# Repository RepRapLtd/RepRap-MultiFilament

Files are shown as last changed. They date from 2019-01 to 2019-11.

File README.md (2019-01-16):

# RepRap-MultiFilament
Multi filament drive for RepRap and other FFF printers

The drive has three components:

  1. Multi-drive - a pinch-wheel drive for multiple filaments driven by a single stepper and a small DC motor.
  2. Guillotine - a device that cuts filament driven by the same small DC motor.
  3. Filament-Y - a passive device that merges feeds of filament into a single Bowden channel.

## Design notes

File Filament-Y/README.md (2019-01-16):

# Filament-Y
A design for a 3D printer filament merging Y for multiple-material RepRaps

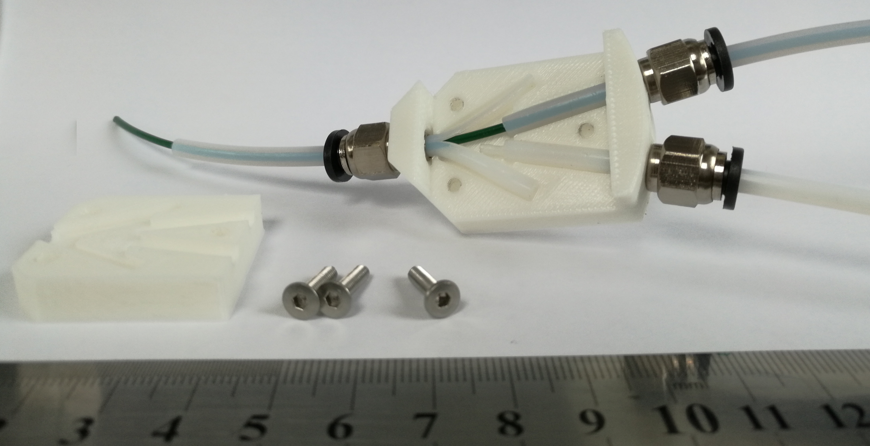
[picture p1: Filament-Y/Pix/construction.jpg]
How it goes together


This design is based on a wonderfully simple idea from Martin Zeman (see: https://www.thingiverse.com/thing:3039887).  It is easy to print, to construct, and to put together.  In operation it works very smoothly with low friction.

Two input 4mm PTFE Bowden feeds come straight through the pneumatic fittings on the right of the picture (like these: https://reprapltd.com/shop/pneumatic-fitting/ ; make sure you get the ones where the tube goes right through).  You split the end of the output tube down the middle to a depth of 20mm then push it through, guiding the two halves of the split to their retaining slots left and right.  Finally screw the top down with three 12mm M3 countersunk screws.  These self-tap into the base.

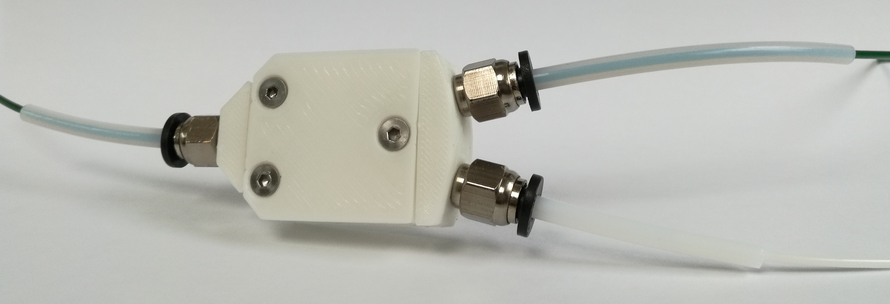
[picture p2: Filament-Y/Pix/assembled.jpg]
Assembled


Here it is assembled.

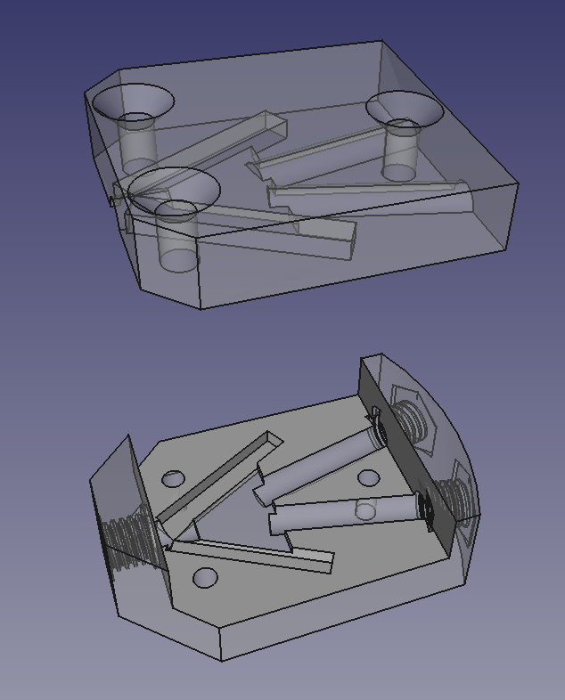
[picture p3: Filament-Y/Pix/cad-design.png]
CAD design


The CAD design was done in FreeCAD (https://www.freecadweb.org/).

You can, of course, chain these together to merge as many filament streams as you wish.

This is the first in a set of modular designs that together will form a multi-filament drive system.  The idea is that you will be able to put them together to form a drive system that will be an add on to any system to feed into a single nozzle.  All the system will need to be able to do is to drive one stepper for them all, and send either serial data or a number of parallel bits to give the number of filaments (1 bit: 2 filaments; 2 bits 4 and so on).

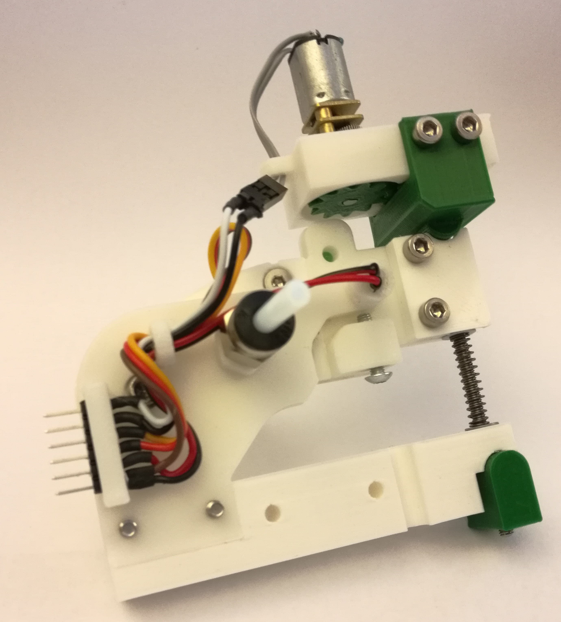
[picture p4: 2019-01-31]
Pix/wired-guillotine.jpg

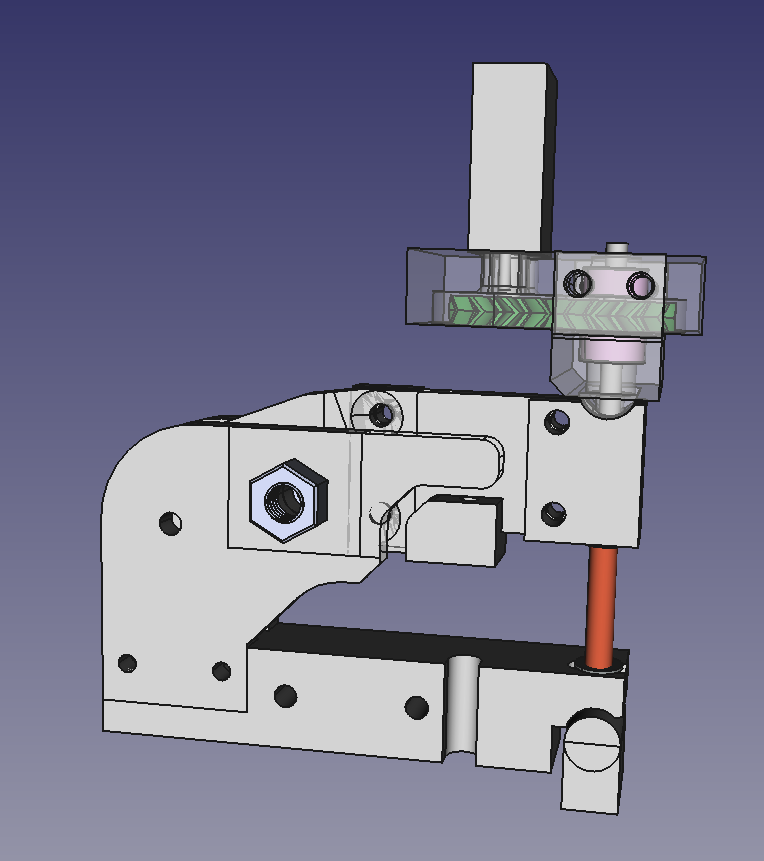
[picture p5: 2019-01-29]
Pix/cad-guillotine.png

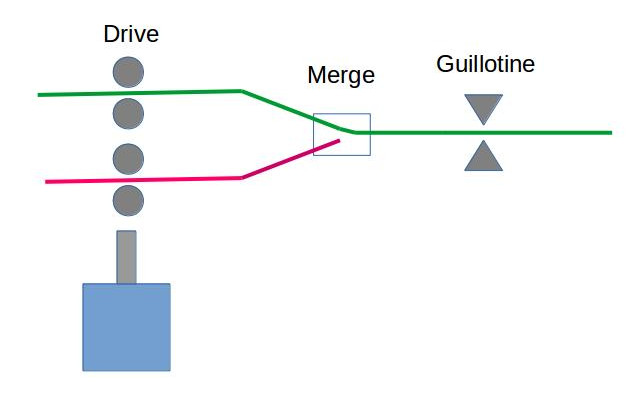
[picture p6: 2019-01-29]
Pix/how-it-works.jpg

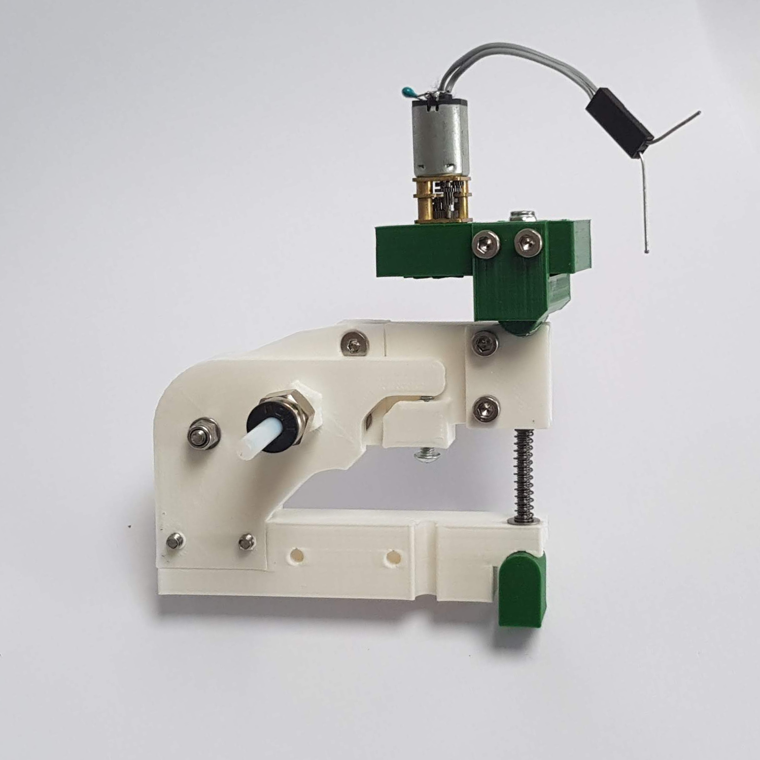
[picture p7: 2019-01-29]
Pix/guillotine-photo.jpg

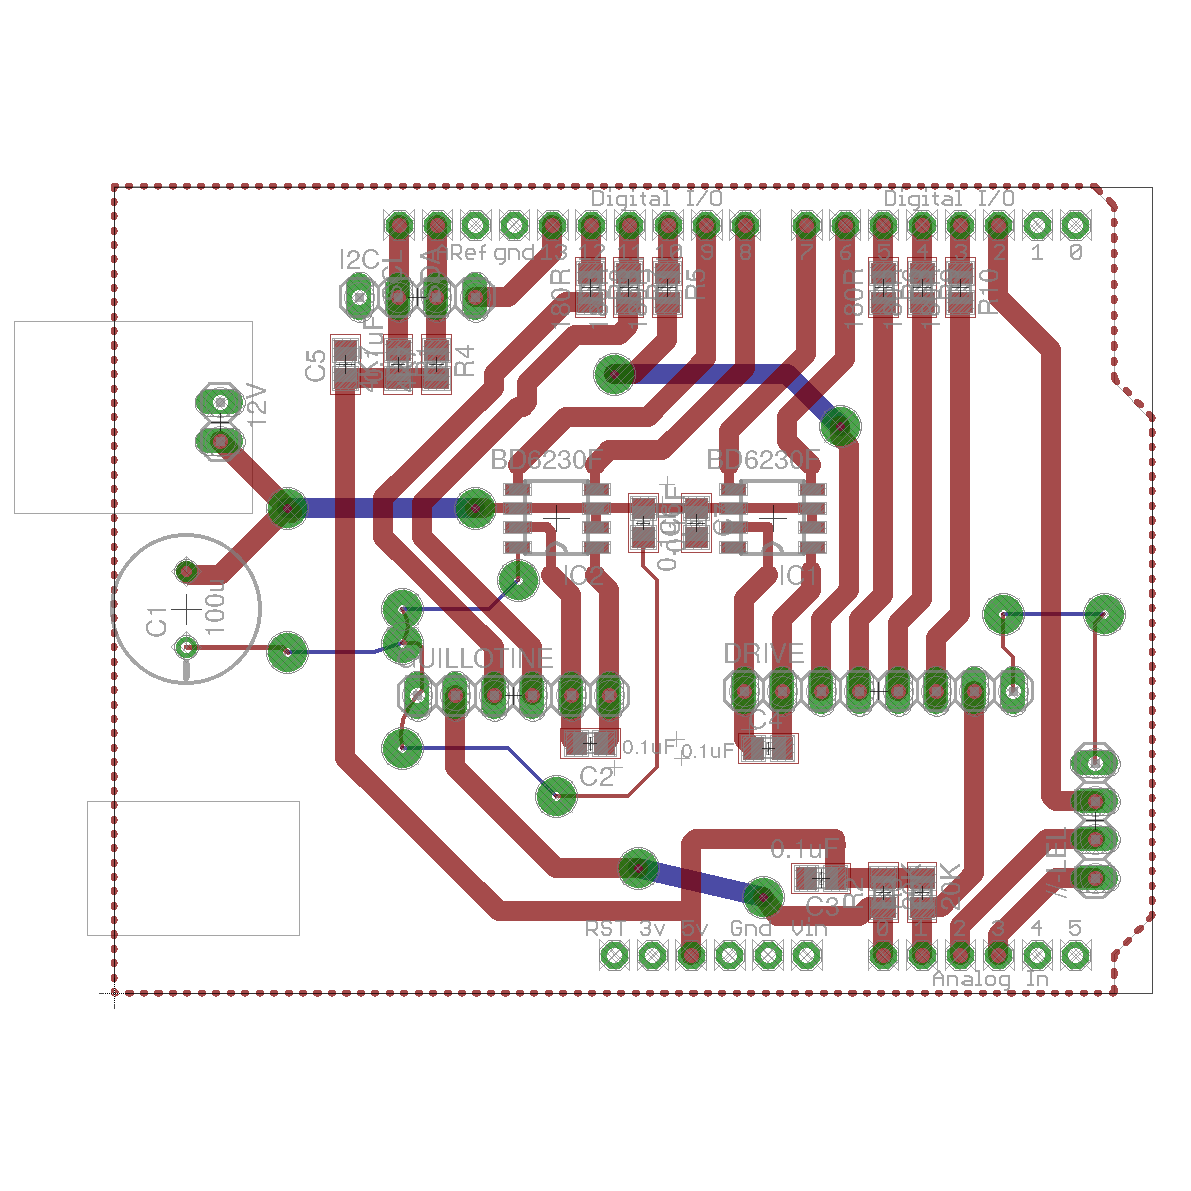
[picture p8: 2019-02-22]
Pix/circuit.png

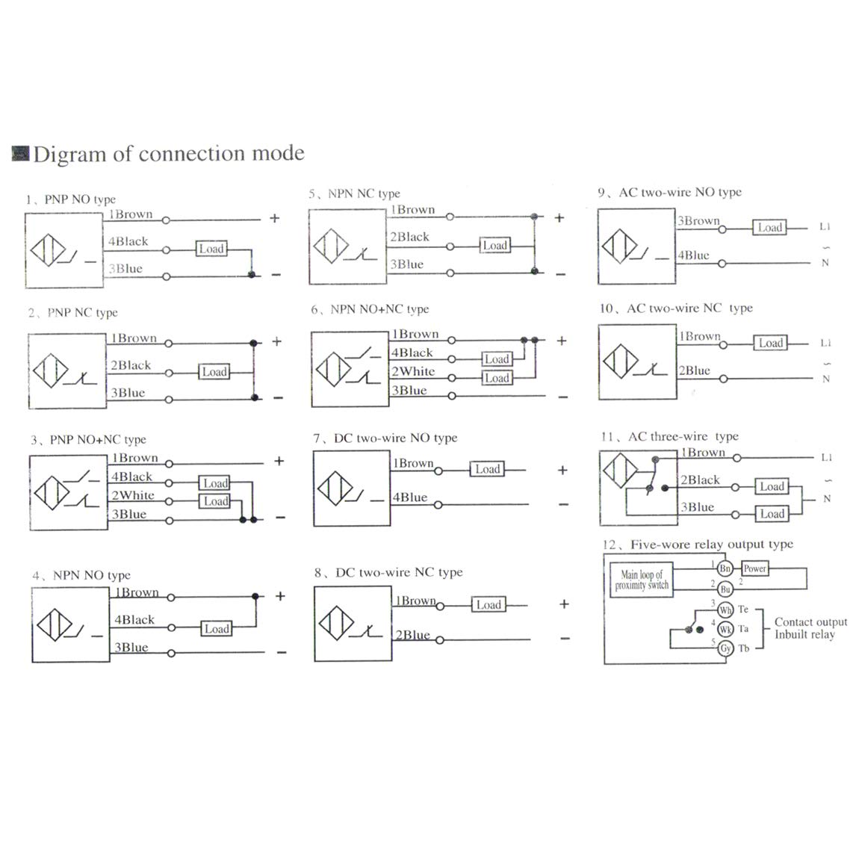
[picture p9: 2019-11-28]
Prusa/mag-sensor2.jpg

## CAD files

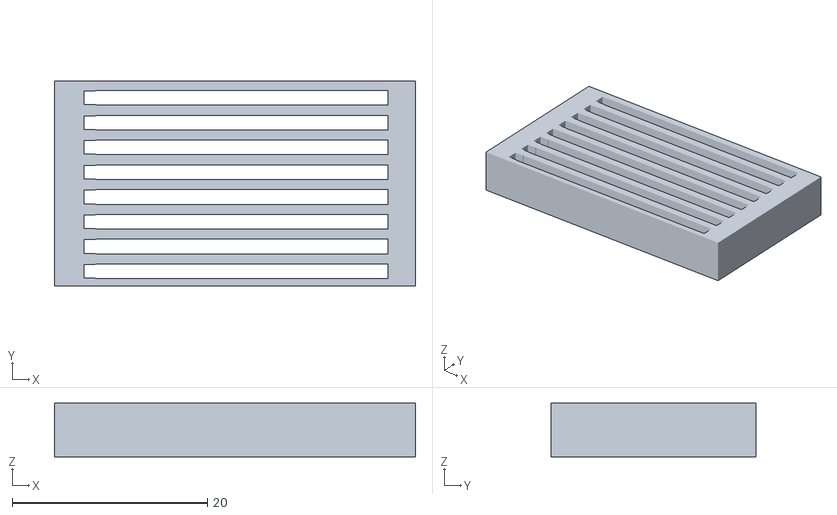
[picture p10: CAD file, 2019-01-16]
Experiment-and-tests/V3 1.2 Main Body.stl
37.0 x 21.0 x 5.50

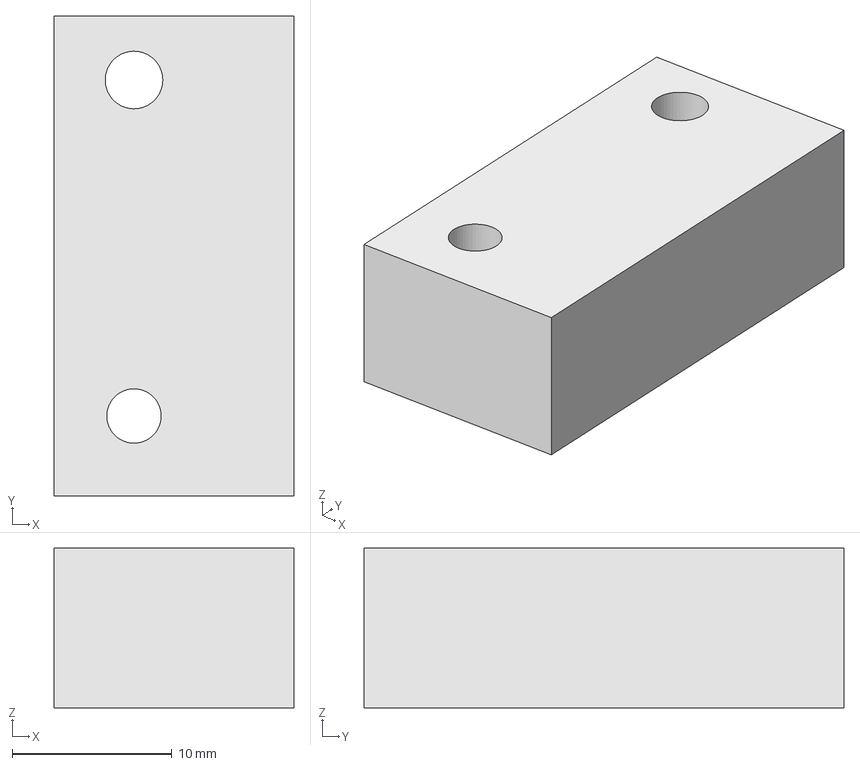
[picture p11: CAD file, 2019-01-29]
Experiment-and-tests/photo-led-test.fcstd
15.0 x 30.0 x 10.0 mm

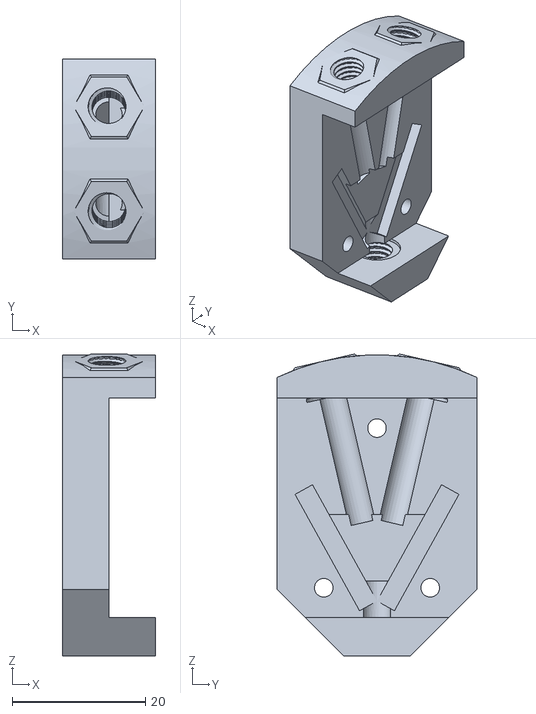
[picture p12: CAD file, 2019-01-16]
Filament-Y/Mechanics/STLs/Y-base.stl
14.0 x 30.0 x 45.4

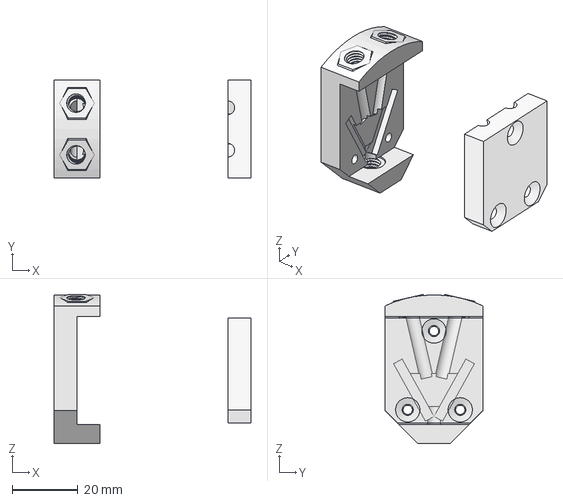
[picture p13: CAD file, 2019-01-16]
Filament-Y/Mechanics/y.fcstd
60.0 x 30.0 x 45.4 mm
base
top

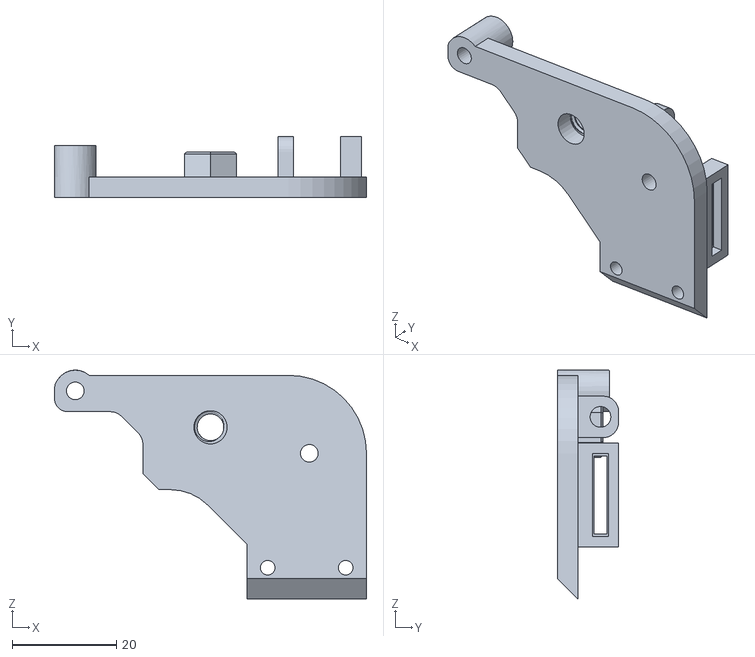
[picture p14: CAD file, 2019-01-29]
Guillotine/Mechanics/STLs/bearing-support-2.stl
60.0 x 11.8 x 44.0

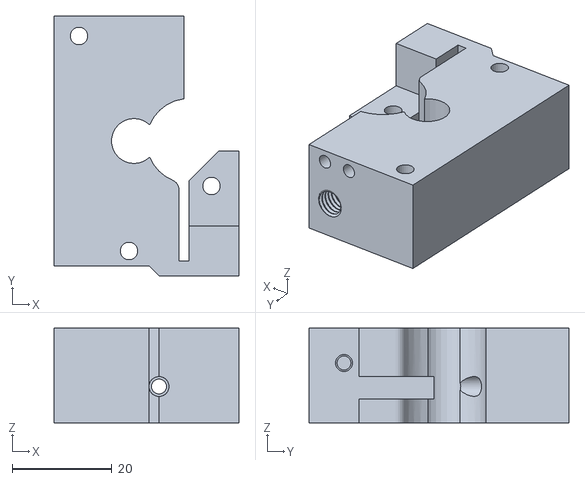
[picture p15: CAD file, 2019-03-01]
Multi-drive/Mechanics/STLs/drive-block.stl
37.0 x 52.0 x 19.0

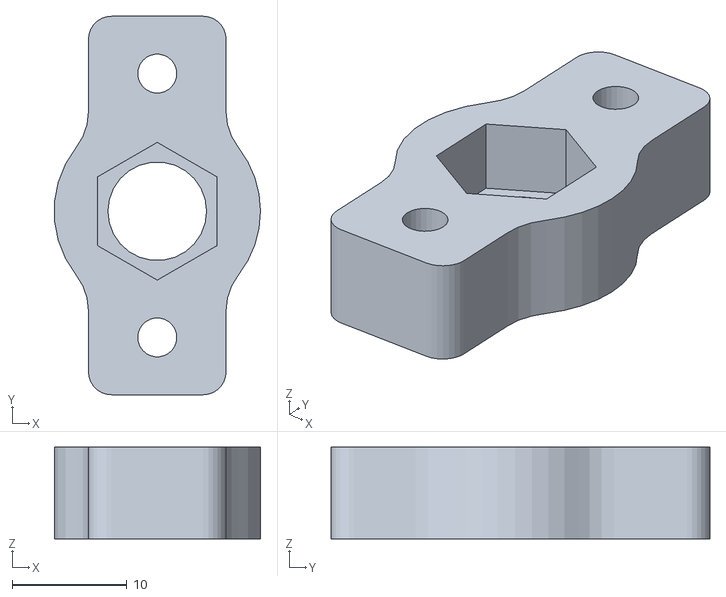
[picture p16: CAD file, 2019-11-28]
Prusa/pneumatic-holder.stl
18.0 x 33.0 x 8.00

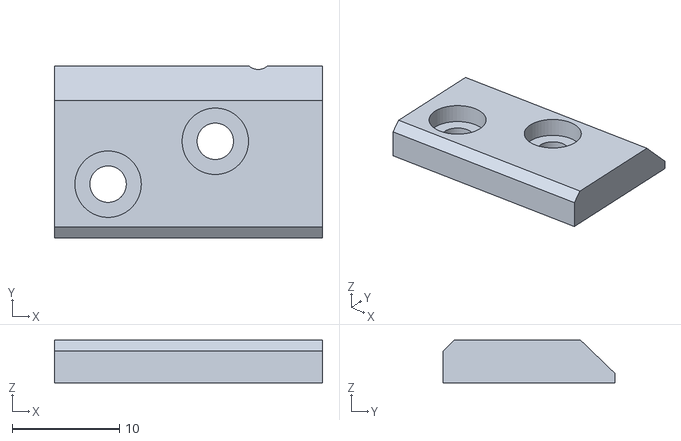
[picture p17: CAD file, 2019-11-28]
Prusa/Prusa MMU/STLs/mmu2-blade-holder.stl
25.0 x 16.0 x 4.00

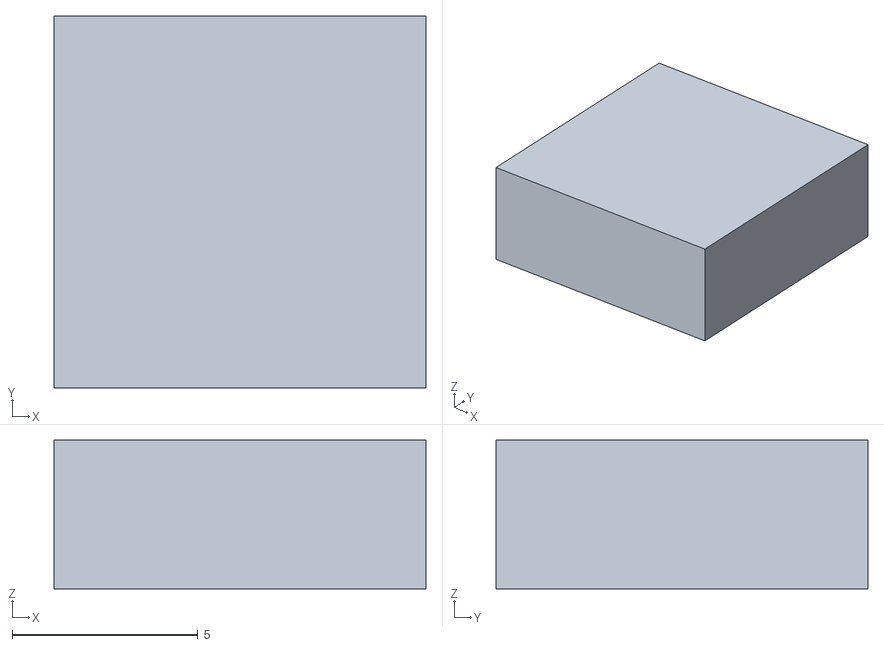
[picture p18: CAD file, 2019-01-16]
Experiment-and-tests/simple-testblock-green.stl
10.0 x 10.0 x 4.00

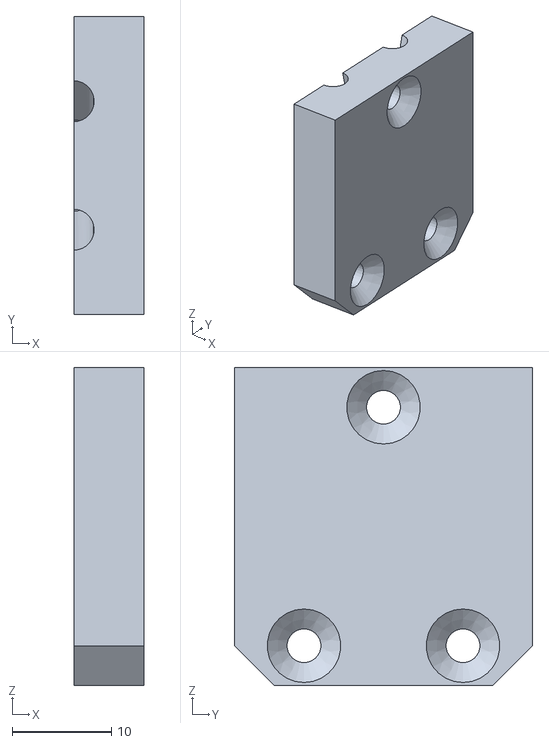
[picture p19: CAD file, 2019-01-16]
Filament-Y/Mechanics/STLs/Y-top.stl
7.00 x 30.0 x 32.0

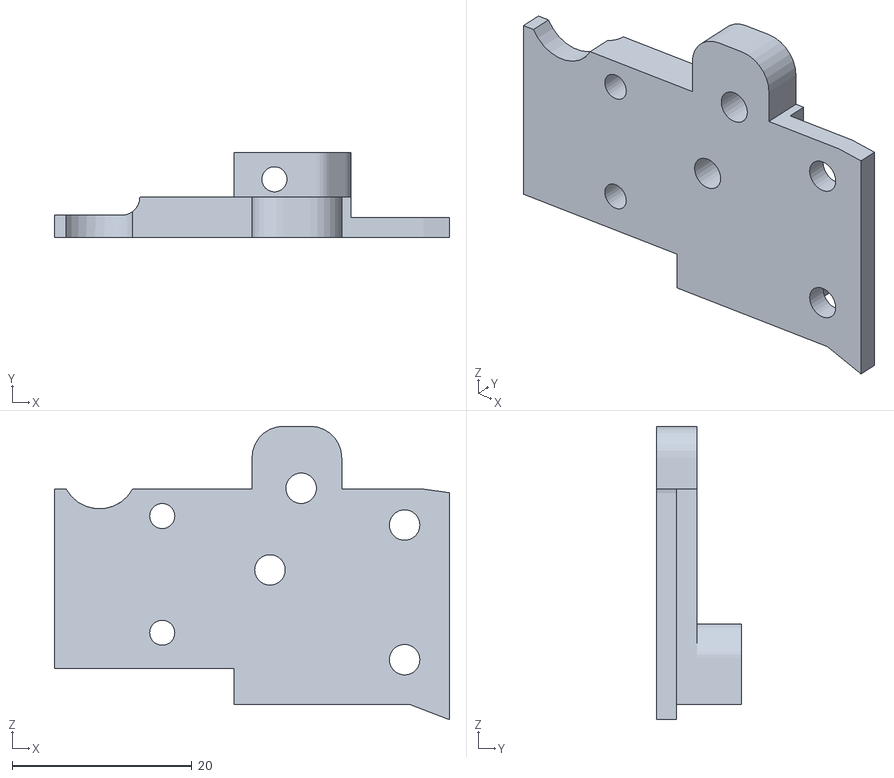
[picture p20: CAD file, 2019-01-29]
Guillotine/Mechanics/STLs/cutting-arm-extension.stl
44.0 x 9.50 x 32.7

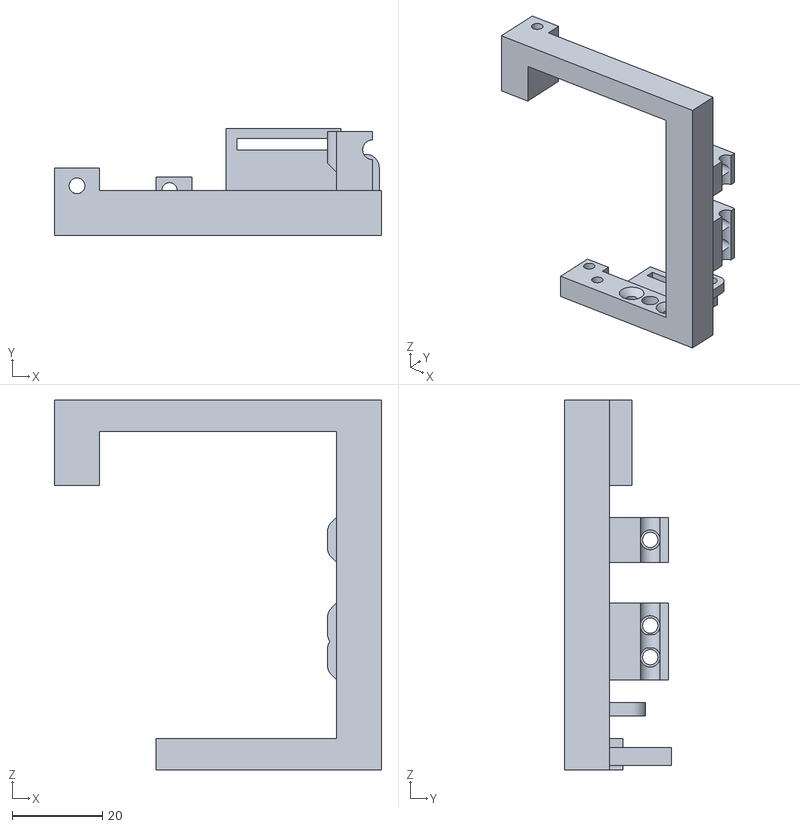
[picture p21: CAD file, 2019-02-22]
Multi-drive/Mechanics/STLs/track.stl
72.5 x 23.7 x 82.0

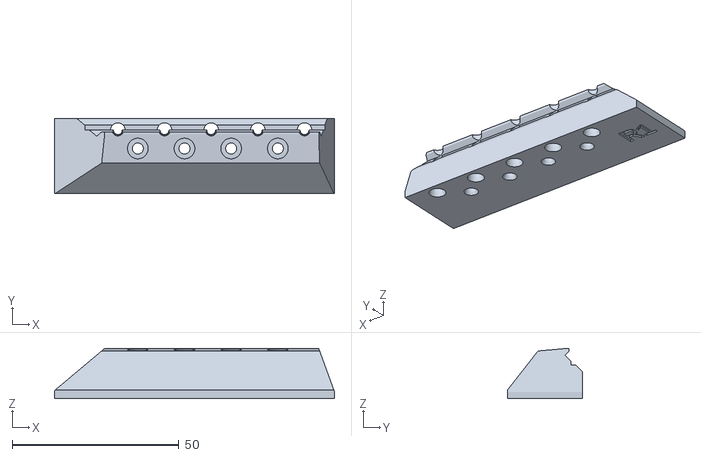
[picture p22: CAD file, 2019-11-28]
Prusa/Prusa MMU/STLs/mmu2-front-PTFE-holder.stl
84.0 x 22.5 x 15.0

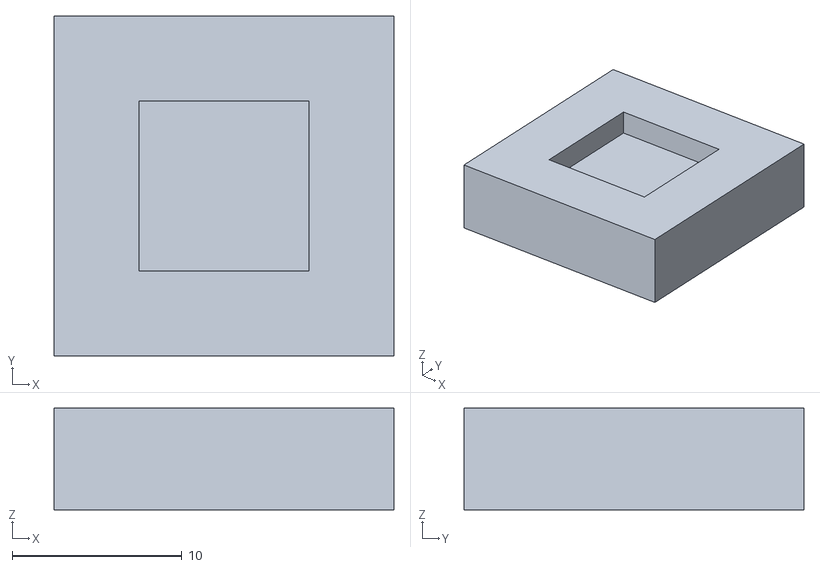
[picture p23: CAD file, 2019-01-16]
Experiment-and-tests/simple-testblock-white.stl
20.0 x 20.0 x 6.00

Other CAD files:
Experiment-and-tests/V2 1.6 Main Body.stl
Experiment-and-tests/V1 0.8 Main Body.stl
Guillotine/Mechanics/STLs/clamp-plate.stl
Multi-drive/Mechanics/STLs/motor-gearbox-mount.stl
Experiment-and-tests/External Thread.stp
Experiment-and-tests/Internal thread.stp
Experiment-and-tests/Test Piece V1 0.8.fcstd
Experiment-and-tests/Test Piece V2 1.6.fcstd
Experiment-and-tests/Test Piece V3 1.2.fcstd
Experiment-and-tests/V1 0.8 Conducting Filament.stl
Experiment-and-tests/V2 1.6 Conducting Filament.stl
Experiment-and-tests/V3 1.2 Conducting Filament.stl
Experiment-and-tests/force-test.fcstd
Experiment-and-tests/photo-led-test.stl
Guillotine/Mechanics/STLs/Legacy/bearing-clamp.stl
Guillotine/Mechanics/STLs/Legacy/cut-holder-arm.stl
Guillotine/Mechanics/STLs/Legacy/cut-holder-base.stl
Guillotine/Mechanics/STLs/Legacy/cut-lever-block.stl
Guillotine/Mechanics/STLs/Legacy/cut-lever.stl
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

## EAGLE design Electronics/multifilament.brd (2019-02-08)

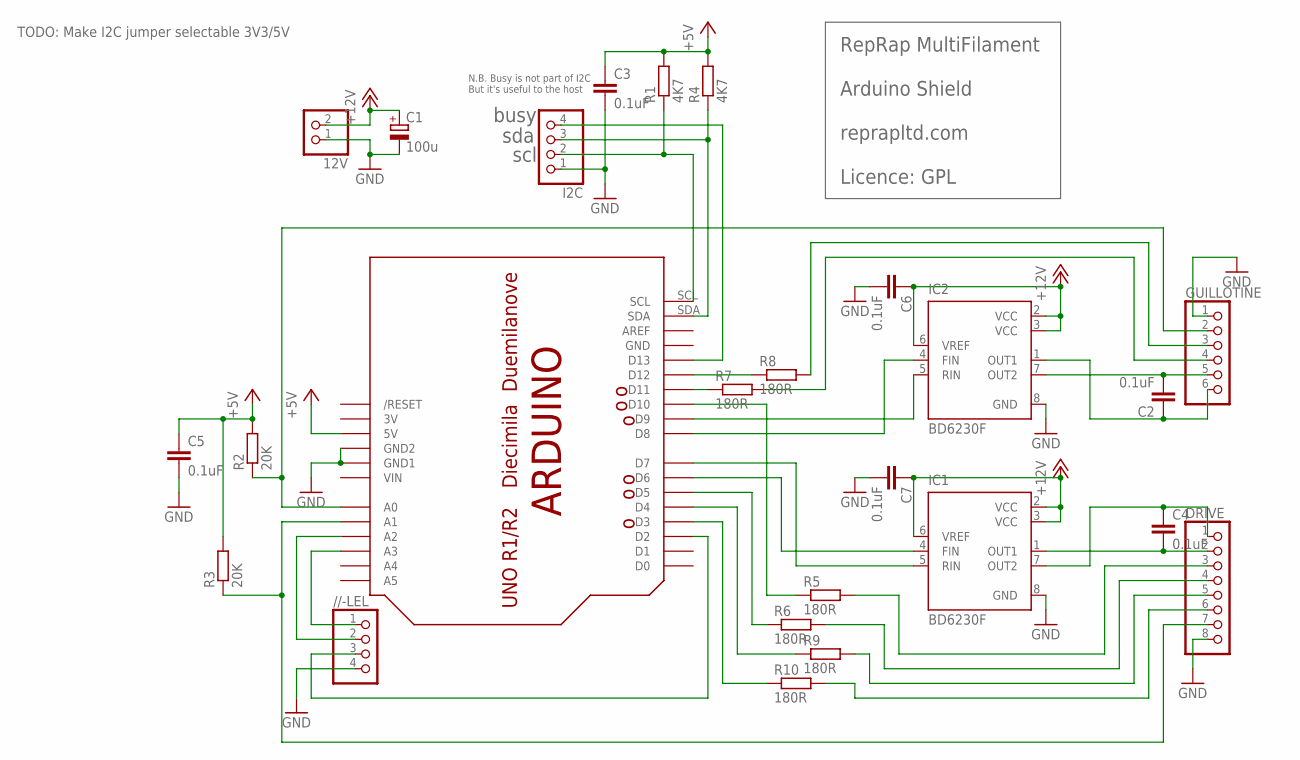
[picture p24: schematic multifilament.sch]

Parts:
12V: PINHD-1X2; 1X02
//-LEL: PINHD-1X4; 1X04
C1: 100u; SANYO-OSCON_9F
C2, C3, C4, C5, C6, C7: 0.1uF; C0805
DRIVE: PINHD-1X8; 1X08
GUILLOTINE: PINHD-1X6; 1X06
I2C: PINHD-1X4; 1X04
IC1, IC2: BD6230F; SOP8
R1, R4: 4K7; M0805
R2, R3: 20K; M0805
R5, R6, R7, R8, R9, R10: 180R; M0805
U$1: ARDUINO-BPLACE

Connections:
3V: U$1.3V
+5V: C3.1, C5.1, R1.2, R2.2, R3.2, R4.2, U$1.5V
+12V: 12V.2, C1.+, C6.1, C7.1, IC1.2 (VCC), IC1.3 (VCC), IC1.6 (VREF), IC2.2 (VCC), IC2.3 (VCC), IC2.6 (VREF)
GND: 12V.1, //-LEL.4, C1.-, C3.2, C5.2, C6.2, C7.2, DRIVE.8, GUILLOTINE.1, I2C.1, IC1.8 (GND), IC2.8 (GND), U$1.GND, U$1.GND1, U$1.GND2
unnamed: I2C.2, R1.1, U$1.SCL
unnamed: GUILLOTINE.2, R2.1, U$1.A0
unnamed: C2.2, GUILLOTINE.5, IC2.7 (OUT2)
unnamed: C4.2, DRIVE.2, IC1.1 (OUT1)
unnamed: R6.1, U$1.D5
unnamed: IC1.4 (FIN), U$1.D6
unnamed: IC1.5 (RIN), U$1.D7
unnamed: IC2.4 (FIN), U$1.D8
unnamed: I2C.3, R4.1, U$1.SDA
unnamed: DRIVE.7, R3.1, U$1.A1
unnamed: IC2.5 (RIN), U$1.D9
unnamed: I2C.4, U$1.D13
unnamed: GUILLOTINE.3, R8.2
unnamed: R7.1, U$1.D11
unnamed: GUILLOTINE.4, R7.2
unnamed: R8.1, U$1.D12
unnamed: R5.1, U$1.D10
unnamed: DRIVE.3, R5.2
unnamed: DRIVE.4, R6.2
unnamed: R9.1, U$1.D4
unnamed: DRIVE.5, R9.2
unnamed: R10.1, U$1.D3
unnamed: DRIVE.6, R10.2
unnamed: //-LEL.2, U$1.A2
unnamed: //-LEL.1, U$1.A3
unnamed: //-LEL.3, U$1.D2
unnamed: C4.1, DRIVE.1, IC1.7 (OUT2)
unnamed: C2.1, GUILLOTINE.6, IC2.1 (OUT1)
VIN: U$1.VIN

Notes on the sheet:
RepRap MultiFilament Arduino Shield reprapltd.com Licence: GPL
busy
sda
scl
N.B. Busy is not part of I2C But it's useful to the host
TODO: Make I2C jumper selectable 3V3/5V

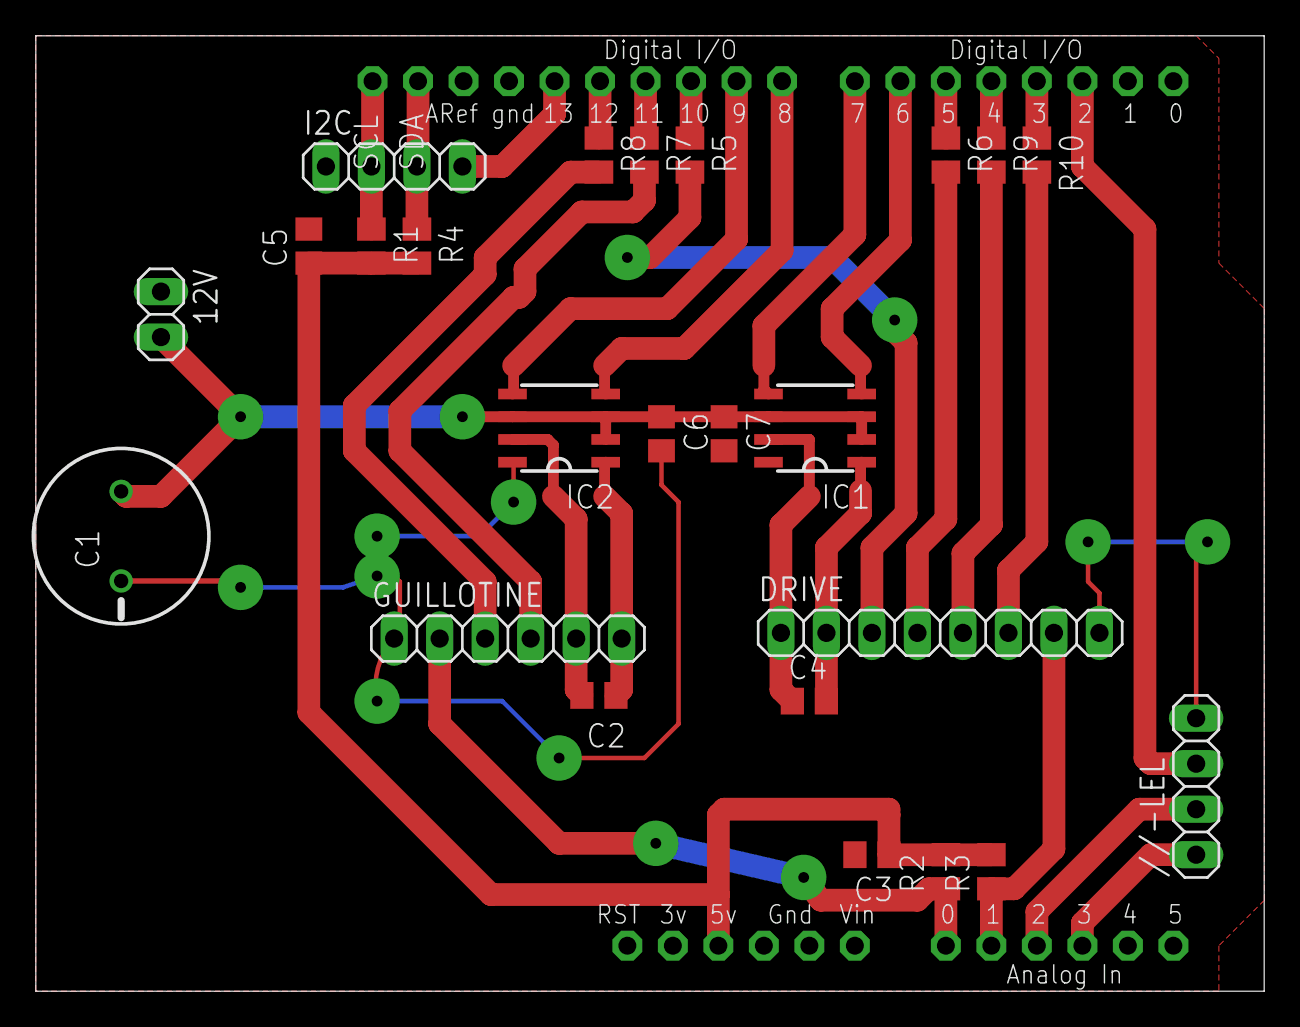
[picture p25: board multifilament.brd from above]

Board: 2 copper layers, 68.6 x 53.3 mm, 25 parts (0 on the bottom side), 31 nets.

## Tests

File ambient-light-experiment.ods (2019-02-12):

Dark | Light | diff
31 | 28 | 3 | 13.2340672 | 10.2340672 | 25.6255748
38 | 30 | 8 | 16.1317788 | 8.1317788
48 | 32 | 16 | 20.2212508 | 4.2212508
124 | 49 | 75 | 49.3744252 | 25.6255748
318 | 195 | 123 | 108.3501148 | 14.6498852
493 | 345 | 148 | 142.5131248 | 5.4868752
548 | 419 | 129 | 149.5208508 | 20.5208508
577 | 445 | 132 | 152.4977008 | 20.4977008
731 | 563 | 168 | 159.9977472 | 8.0022528
756 | 588 | 168 | 159.8960572 | 8.1039428
788 | 645 | 143 | 159.2281788 | 16.2281788
808 | 640 | 168 | 158.5041628 | 9.4958372
864 | 694 | 170 | 155.2222492 | 14.7777508
1003 | 870 | 133 | 139.0855168 | 6.0855168

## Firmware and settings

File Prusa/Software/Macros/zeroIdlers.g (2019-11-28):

; Zero the idler bearings

M906 X800 Y800 Z800 E800:800:800:500
T3
M83
G1 E-10 F500
G92 E0:0:0:0
M906 X800 Y800 Z800 E800:800:800:800

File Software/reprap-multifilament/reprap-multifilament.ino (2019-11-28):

/*
   RepRap MultiFilament Arduino Control Program

   This controls the RepRap Multifilament drive using
   a shield for the Arduino Uno.

   Adrian Bowyer

   RepRap Ltd
   http://reprapltd.com

   Github: https://github.com/RepRapLtd/RepRap-MultiFilament

   Licence: GPL

   7 February 2019
*/

// Arduino Uno Pins

// BD6231 Motor H-bridge chips

const unsigned char driveFIN = 6;      // PWM
const unsigned char driveRIN = 7;
const unsigned char guillotineFIN = 8;
const unsigned char guillotineRIN = 9; // PWM

// Optosensors

const unsigned char guillotinePT = A0;  // Phototransistor
const unsigned char drivePT = A1;       // Phototransistor
const int driveLEDs = 4;
const unsigned char driveLED[4] = {3, 4, 5, 10};
const int guillotineLEDs = 2;
const unsigned char guillotineLED[2] = {12, 11};
const int drive = 1;
const int guillotine = 2;
const int forward = 1;
const int reverse = 2;
//const int findThreshold = 100;
//const int moveThreshold = 140;
const long maxDriveMoveTime = 45000;
const long maxGuillotineMoveTime = 16000;
const int fineTuneDrive = 3000;
const int fineTuneGuillotine = 1500;
const int darkThreshold = 400;

/*
 * The expected difference between light and dark reduces as ambient light
 * increases.  This is a quadratic approximation to that behaviour:
 * 
 *    Difference = -0.0002948xdark_level^2 + 0.4343xdark_level + 0.05407
 */

const float a0 = 0.05407;
const float a1 = 0.4343;
const float a2 = -0.0002948;

// The acceptable error band

const int diffError = 25;

// Status pin

const unsigned char busy = 13;     // Also the on-board LED
const unsigned char debugPin = 2;  // On the //-lel port; Ground this pin to turn debugging on

// PWM

unsigned char guillotineForwardPWM = 170;
unsigned char guillotineReversePWM = 80;
unsigned char driveForwardPWM = 80;
unsigned char driveReversePWM = 120;
int lastDirection;

bool debug;

int device = guillotine;

void Busy(bool b)
{
  digitalWrite(busy, b);
}

/*
   Control the movement of the motors
*/
void Brake(int device)
{
  if (device == drive)
  {
    digitalWrite(driveFIN, 1);
    digitalWrite(driveRIN, 1);
  } else
  {
    digitalWrite(guillotineFIN, 1);
    digitalWrite(guillotineRIN, 1);
  }
}

void Forward(int device)
{
  lastDirection = forward;
  if (device == drive)
  {
    analogWrite(driveFIN, driveForwardPWM);
    digitalWrite(driveRIN, 0);
  } else
  {
    digitalWrite(guillotineFIN, 1);
    analogWrite(guillotineRIN, 255 - guillotineForwardPWM);
  }
}

void Reverse(int device)
{
  lastDirection = reverse;
  if (device == drive)
  {
    analogWrite(driveFIN, 255 - driveReversePWM);
    digitalWrite(driveRIN, 1);
  } else
  {
    digitalWrite(guillotineFIN, 0);
    analogWrite(guillotineRIN, guillotineReversePWM);
  }
}



/*
 * Set up a LED light reading with the right phototransistor and LED
 */
void GetTransistorAndLED(int device, int ledNumber, unsigned char& pt, unsigned char& led)
{
  if (device == drive)
  {
    pt = drivePT;
    led = driveLED[ledNumber];
  } else
  {
    pt = guillotinePT;
    led = guillotineLED[ledNumber];
  }  
}

/*
   Get the difference between dark and light for a LED/phototransistor pair.
   Note dark readings are larger than light ones.
*/
int differentialPhoto(int device, int ledNumber)
{
  unsigned char pt;
  unsigned char led;
  GetTransistorAndLED(device, ledNumber, pt, led);

  int result = analogRead(pt);
  digitalWrite(led, 1);
  result = result - analogRead(pt);
  digitalWrite(led, 0);
  return result;
}

/*
 * Are we at a given position?
 * The criterion is LED on/off difference is diffError greater than the expected value.
 */
bool AtLEDPosition(int device, int ledNumber)
{
  unsigned char pt;
  unsigned char led;
  GetTransistorAndLED(device, ledNumber, pt, led);

  int dark = analogRead(pt);
  digitalWrite(led, 1);
  int diff = dark - analogRead(pt);
  digitalWrite(led, 0);
  if((dark < darkThreshold) && debug)
  {
    Serial.print("Background light level (");
    Serial.print(dark);
    Serial.println(") is too bright.");
  }
  //float expectedDiff = (float)dark;
  //expectedDiff = a2*expectedDiff*expectedDiff + a1*expectedDiff + a0;
  //return diff > ((int)(0.5 + expectedDiff) - diffError);
  return diff > 50;  
}

/*
 * Report the status of a LED-phototransistor pair.
 * Mainly for debugging
 */
void ReportDarkAndLight(int device, int ledNumber)
{
  unsigned char pt;
  unsigned char led;
  GetTransistorAndLED(device, ledNumber, pt, led);

  int dark = analogRead(pt);
  digitalWrite(led, 1);
  int light = analogRead(pt);
  digitalWrite(led, 0);
  Serial.print("Dark: ");
  Serial.print(dark);
  Serial.print(", light: ");
  Serial.print(light);
  Serial.print(", diff: ");
  Serial.println(dark - light);  
}

/*
   Find what position the device is at. -1 means its phototransistor
   is not opposite any LED.  Note this is for when the device is stationary; it won't
   work well when the device is moving.
*/
int FindPosition(int device)
{
  int leds;

  if (device == drive)
  {
    leds = driveLEDs;
  } else
  {
    leds = guillotineLEDs;
  }

  int led = 0;
  while(led < leds && !AtLEDPosition(device, led))
  {
    led++;
  }

  if(led >= leds)
  {
    led = -1;
  }

  if (debug)
  {
    Serial.print(" pos: ");
    Serial.println(led);
  }
  return led;
}

/*
   Continue the last movement a bit to maximise the phototransistor output and
   so centre the LED and phototransistor opposite each other.
*/
void FineTune(int device, int led)
{
    int runTime = fineTuneDrive;
    if(device == guillotine)
    {
      runTime = fineTuneGuillotine;
    }
    
    if(lastDirection == forward)
    {
      Forward(device);
    } else
    {
      Reverse(device);
    }
    
    delay(runTime);
    Brake(device);
}

/*
   Drive the device to a given position.
*/
int SeekPosition(int device, int led)
{
  if (debug)
  {
    Serial.print("Seeking position ");
    Serial.print(led);
    Serial.print(" on device ");
    Serial.println(device);
  }

  long maxMoveTime = maxGuillotineMoveTime;

  if(device == drive)
  {
    maxMoveTime = maxDriveMoveTime;
  }

  int pos = FindPosition(device);
  if (pos < 0)
  {
    if (debug)
    {
      Serial.println("Seeking a position from an unknown position!");
    }
    return;
  }

  if (pos == led)
  {
    return;
  }

  if (pos > led)
  {
    Reverse(device);
  } else
  {
    Forward(device);
  }

  long t = (long)millis();
  bool notThere = true;

  while ((((long)millis() - t) < maxMoveTime) && notThere)
  {
    if(AtLEDPosition(device, led))
    {
      notThere = false;
    }
    delay(10);
  }
  
  if (debug)
  {
    if(notThere)
    {
      Serial.println("Time out on movement.");
    }
  }
  FineTune(device, led);
}

void Drive(int pos)
{
  Busy(true);
  SeekPosition(drive, pos);
  Busy(false);
}

void Cut()
{
  Busy(true);
  SeekPosition(guillotine, 1);
  SeekPosition(guillotine, 0);
  Reverse(guillotine);
  delay(2500);
  Brake(guillotine);
  Busy(false); 
}

void Prompt()
{
  if(!debug)
    return;

  Serial.println("\n 0-9: Seek drive position n.");
  Serial.println(" f: Forwad for 0.5s.");
  Serial.println(" r: Reverse for 0.5s.");
  Serial.println(" F: Forwad for 2s.");
  Serial.println(" R: Reverse for 2s.");
  Serial.println(" c: Guillotine cut cycle.");
  Serial.println(" p: Print device position.");
  Serial.println(" ln: Report light levels at position n.");
  Serial.println(" d: Switch device to drive.");
  Serial.println(" g: Switch device to guillotine.");
  Serial.print(" The current device is the ");
  if(device == drive)
    Serial.println("drive.\n");
  else
    Serial.println("guillotine.\n");
}

void Interpreter()
{
  if(!debug)
    return;

  if (!Serial.available())
    return;
    
  int p;
  
  int c = Serial.read();
  if(isdigit(c))
  {
    Drive(c - '0');
  } else
  {
    switch (c)
    {
      case ' ':
      case '\t':
      case '\n':
        break;

      case 'f':
        Forward(device);
        delay(500);
        Brake(device);
        break;

      case 'r':
        Reverse(device);
        delay(500);
        Brake(device);
        break;

      case 'F':
        Forward(device);
        delay(2000);
        Brake(device);
        break;

      case 'R':
        Reverse(device);
        delay(2000);
        Brake(device);
        break;

      case 'c':
        Cut();
        break;

      case 'p':
        p = FindPosition(device);
        Serial.print("Position: ");
        Serial.println(p);
        break;

      case 'l':
        while(!Serial.available());
        c = Serial.read();
        p = c - '0';
        ReportDarkAndLight(device, p);
        break;

      case 'd':
        device = drive;
        Serial.println("Device is now the drive.");
        break;

      case 'g':
        device = guillotine;
        Serial.println("Device is now the guillotine.");
        break;

      default:
        if (debug)
        {
          Serial.print("Illegal command: ");
          Serial.println((char)c);
          Prompt();
        }
    }
  }  
}

void setup()
{
  pinMode(busy, OUTPUT);
  Busy(true);

  pinMode(driveFIN, OUTPUT);
  pinMode(driveRIN, OUTPUT);
  pinMode(guillotineFIN, OUTPUT);
  pinMode(guillotineRIN, OUTPUT);
  Brake(drive);
  Brake(guillotine);

  for (int i = 0; i < driveLEDs; i++)
  {
    pinMode(driveLED[i], OUTPUT);
    digitalWrite(driveLED[i], 0);
  }
  for (int i = 0; i < guillotineLEDs; i++)
  {
    pinMode(guillotineLED[i], OUTPUT);
    digitalWrite(guillotineLED[i], 0);
  }

  pinMode(debugPin, INPUT_PULLUP);
  debug = !digitalRead(debugPin);
  pinMode(guillotinePT, INPUT);
  pinMode(drivePT, INPUT);

  Serial.begin(9600);
  if (debug)
  {
    Serial.println("\nRepRap MultiFilament\n");
  }

  Prompt();

}

void loop()
{

  Interpreter();
  debug = !digitalRead(debugPin);
}

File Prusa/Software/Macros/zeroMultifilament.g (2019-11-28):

; Zero the selector and idler bearings

M906 X800 Y800 Z800 E800:800:600:500
T2 P0
M83
G1 E-75 F500
M82
T3 P0
M83
G1 E-10 F500
G92 E0:0:0:0
M82
M906 X800 Y800 Z800 E800:800:800:800

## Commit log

2019-01-16 First commit.
    [External Thread.stp, Internal thread.stp, Test Piece V1 0.8.fcstd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]
2019-01-16 File reorganising.
    [External Thread.stp, Internal thread.stp, Test Piece V1 0.8.fcstd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]
2019-01-18 New guillotine. WIP.
    [base.stl, bearing-clamp.stl, calculator.ods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]
2019-01-21 New guillotine design fininshed?
    [base-and-mount.stl, base.stl, bearing-support-1.stl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]
2019-01-24 Improved design of guillotine arm.
    [calculator.ods, cutting-arm-extension.stl, top-slot-plate.stl]
2019-01-29 Guillotine with photosensors added.
    [bearing-support-2.stl, clamp-plate.stl, cutting-arm-extension.stl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]
2019-01-31 Guillotine sensor wiring finished (?).
2019-02-06 First design of Arduino Uno shield electronics.
    [multifilament.brd, multifilament.sch]
2019-02-08 First working version of guillotine software.
    [multifilament.brd, multifilament.sch]
2019-02-11 Tuning up the light detection.
    [ambient-light-experiment.ods]
2019-02-12 Parameters adjusted in software - first working version.
    [ambient-light-experiment.ods]
2019-02-22 Improving the multi-drive design. Making the clamp wheel adjustable.
    [bearing-clamp.g, bearing-clamp.stl, drive-block.stl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]
2019-03-01 Improved filament clamp design. All GCode folders gone.
    [bearing-clamp.g, drive-block.stl, track-etc.g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]
2019-11-28 Making Prusa MMU2 etc a submodule
    [BoM.ods, adapter.g, adapter.stl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]
